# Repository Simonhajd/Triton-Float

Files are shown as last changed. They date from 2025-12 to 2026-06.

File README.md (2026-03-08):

# Triton Float

Development repository for the 2026 Triton Robotics Float.

## Overview

The Triton Float is being developed for the 2026 MATE ROV Pioneer competition (Newfoundland).
This design iteration is approximately 33% smaller than last year's model, while targeting more than 2× performance improvements in speed and significantly increased precision through layered redundancy and sensor feedback systems. It also includes a dedicated LoRa radio as opposed to last year's 4cm wire antenna, which will increase the reliability and robustness of the system.

## Features

Dimensions: 200mm x 4 in diameter.
Buoyancy system: PWM pump ranging from 220mL/min to -220mL/min.

Accuracy Strategy:

- Internal pressure sensor for ballast state verification  
- Pump movement feedback sensor for closed-loop control  
- Pre-calibrated pump flow rate modeling for predictive adjustment
- Additional onboard MCU sensors for reproducible control accuracy

## Hardware / Electrical

- Microcontroller: XIAO nRF52840 Sense  

- Sensors:  
  - XIAO nRF52840 Sense onboard IMU & sensors  
  - Blue Robotics Bar02  
  - Internal pressure sensor  
  - Pump movement sensor  

- Power System:  
  Custom voltage regulation system controlled via relay and magnetic hall-effect sensor on a secondary accessory PCB  

- PCB Revisions:  
  R2 completed, R3 in development

## Mechanical Design

Fusion / CAD link:
🔗 [View Fusion 360 CAD](https://a360.co/4slAPcB)

Notes:
### Structural Considerations:

Cylindrical housing designed to fit within a 4 in diameter constraint

Internal layout arranged to allow operation in the case of flooding (up to ~50-75% of internal volume) while maintaining core electronic functionality.

PCB mounted using tight-tolerance standoffs to prevent movement under vibration and ease serviceability

Layer system used to keep the float intact when the top flange and shell is removed.

### Integration Notes:

Limited internal volume required careful routing of wiring and tubing

Added solderable vias for power, in order to have a secure connection to the battery.

Accessory PCB used to isolate power regulation from main control logic

R3 revision addresses footprint issues and uses a different simpler power system for a working prototype.

## Current Status

- Version / Revision: R2
- In progress: R3, with fixed tracing and the internal pressure sensor.
- Completed: R2.
- Next steps: Testing R3 when it comes in.

## Tools 

- PCB software: KiCad
- CAD software: Fusion 360
- Firmware tools: C++

## Images
Screenshot 2026-02-16 at 4 56 35 PM

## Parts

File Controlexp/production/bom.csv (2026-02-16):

Designator | Footprint | Quantity | Value | LCSC Part #
C1, C3, C7 | 0805 | 3 | 0.1uF
C2, C4, C8 | 0805 | 3 | 10uF
C5 | 0805 | 1 | 10uF, 25V
C6 | 0805 | 1 | 22uF, 6.3V
D1 | 0805 | 1 | RED
J1 | CONN_RF2-04A-T-00-50-G_ADM | 1 | SMA_CONNECTOR
J4 | MOLEX_530470510 | 1 | 530470510
J5 | PinHeader_1x05_P2.54mm_Vertical | 1 | Power Connector
J6 | JST_GH_BM04B-GHS-TBT_1x04-1MP_P1.25mm_Vertical | 1 | Pressure sensor
J7 | PinHeader_1x03_P2.54mm_Vertical | 1 | POWER PROBE
L1 | 0805 | 1 | 2.2uH
R1, R2 | 0805 | 2 | 10k
R3 | 0603 | 1 | 220
R5, R6 | 0603 | 2 | 4.7k
U2 | HOPERF_RFM9XW_THT | 1 | RFM95W
U3 | WSON-8-1EP_2x2mm_P0.5mm_EP0.9x1.6mm_ThermalVias | 1 | TPS62162DSG
U4 | Bosch_LGA-8_3x3mm_P0.8mm_ClockwisePinNumbering | 1 | BME680
U5 | MODULE_113991054 | 1 | XIAO-nRF52840-DIP

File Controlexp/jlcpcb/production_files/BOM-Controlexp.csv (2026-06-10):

Comment | Designator | Footprint | LCSC | Quantity
2.2uH | L2 | L_0805_2012Metric |  | 1
SS34 | D2 | DIOM7959X265N |  | 1
Conn_01x02 | J2 | P-250-202 |  | 1
0.1uF | C1 | C_0805_2012Metric |  | 1
RED | D1 | LED_0805_2012Metric |  | 1
2.2uH | L1 | L_0805_2012Metric |  | 1
10uF | C2 | C_0805_2012Metric |  | 1
530470510 | J4 | MOLEX_530470510 |  | 1
RFM95W |  | HOPERF_RFM9XW_THT |  | 0
Pressure sensor | J6 | JST_GH_BM04B-GHS-TBT_1x04-1MP_P1.25mm_Vertical |  | 1
4.7k | R6 | R_0603_1608Metric |  | 1
TPS62162DSG | U3 | WSON-8-1EP_2x2mm_P0.5mm_EP0.9x1.6mm_ThermalVias |  | 1
10uF | C4 | C_0805_2012Metric |  | 1
0.1uF | C3 | C_0805_2012Metric |  | 1
Conn_Coaxial_Small | J1 | CONN_RF2-04A-T-00-50-G_ADM |  | 1
22uF, 6.3V | C6 | C_0805_2012Metric |  | 1
10uF, 25V | C5 | C_0805_2012Metric |  | 1
4.7k | R5 | R_0603_1608Metric |  | 1
TPS62163DSG | U5 | WSON-8-1EP_2x2mm_P0.5mm_EP0.9x1.6mm_ThermalVias |  | 1
220 | R3 | R_0603_1608Metric |  | 1
220 uF | C9 | C_0805_2012Metric |  | 1
Extra sensor TOP | J10 | JST_GH_BM04B-GHS-TBT_1x04-1MP_P1.25mm_Vertical |  | 1
10uF, 25V | C11 | C_0805_2012Metric |  | 1
LED | J8 | JST_GH_BM04B-GHS-TBT_1x04-1MP_P1.25mm_Vertical |  | 1
100nF | C14 | C_0805_2012Metric |  | 1
Power Connector | J5 | PinHeader_1x05_P2.54mm_Vertical |  | 1
Conn_01x02 | JBUTT1 | PinHeader_1x02_P2.54mm_Vertical |  | 1
220 uF | C10 | C_0805_2012Metric |  | 1
ToF sensor | J7 | JST_GH_BM04B-GHS-TBT_1x04-1MP_P1.25mm_Vertical |  | 1
100nF | C13 | C_0805_2012Metric |  | 1
SN74LVC1T45DBV | U6 | SOT-23-6 |  | 1
BMP388 | U7 | XDCR_BMP388 |  | 1
PWRCONN | J9 | JST_GH_BM03B-GHS-TBT_1x03-1MP_P1.25mm_Vertical |  | 1
XIAO-ESP32-S3-Plus-SMD | U1 | XIAO-ESP32-S3-Plus-SMD |  | 1
22uF, 10V | C12 | C_0805_2012Metric |  | 1
Extra sensor BOTTOM | J11 | JST_GH_BM04B-GHS-TBT_1x04-1MP_P1.25mm_Vertical |  | 1

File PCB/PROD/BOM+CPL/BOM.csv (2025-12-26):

BOM
BOM
BOM
FlightController
Id | Designator | Footprint | Quantity | Comment | Supplier and ref
1 | R3,R1 | R_0402_1005Metric_Pad0.72x0.64mm_HandSolder | 2 | 0.1uF
2 | R4,R2 | R_0402_1005Metric_Pad0.72x0.64mm_HandSolder | 2 | 10uF

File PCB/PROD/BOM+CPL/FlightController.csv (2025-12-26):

Id | Designator | Footprint | Quantity | Designation | Supplier and ref
1 | R3,R1 | R_0402_1005Metric_Pad0.72x0.64mm_HandSolder | 2 | 0.1uF
2 | R4,R2 | R_0402_1005Metric_Pad0.72x0.64mm_HandSolder | 2 | 10uF
3 | R5 | R_0402_1005Metric_Pad0.72x0.64mm_HandSolder | 1 | 10-33 uF
4 | U1 | XIAO-nRF52840-DIP | 1 | nRF52840 (Sense) WAS HERE
5 | U2 | XCVR_RFM95W-868S2 | 1 | RFM95W
6 | J6 | PinHeader_1x03_P2.54mm_Vertical | 1 | Connect The Hall Circuit Here!
7 | J5 | PinHeader_1x05_P2.54mm_Vertical | 1 | Feedback This Side
8 | J4 | PinHeader_1x03_P2.54mm_Vertical | 1 | BATT Reg IC
9 | J3 | PinHeader_1x01_P2.54mm_Vertical | 1 | -
10 | J2 | PinHeader_1x01_P2.54mm_Vertical | 1 | +
11 | TS Better Work | TE_5-1814832-2 | 1 | SMA Connector

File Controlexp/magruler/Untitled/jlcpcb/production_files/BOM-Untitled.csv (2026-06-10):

Comment | Designator | Footprint | LCSC | Quantity
TMAG5273A1QDBVR | U2 | DBV0006A-IPC_A |  | 1
100nF | C3 | C_0201_0603Metric |  | 1
100nF | C2 | C_0201_0603Metric |  | 1
Conn_01x04_Pin | J1 | JST_GH_BM04B-GHS-TBT_1x04-1MP_P1.25mm_Vertical |  | 1
TMAG5273A1QDBVR | U4 | DBV0006A-IPC_A |  | 1
TMAG5273A1QDBVR | U3 | DBV0006A-IPC_A |  | 1
220 | R3 | R_0603_1608Metric |  | 1
RED | D1 | LED_0805_2012Metric |  | 1
100nF | C1 | C_0201_0603Metric |  | 1

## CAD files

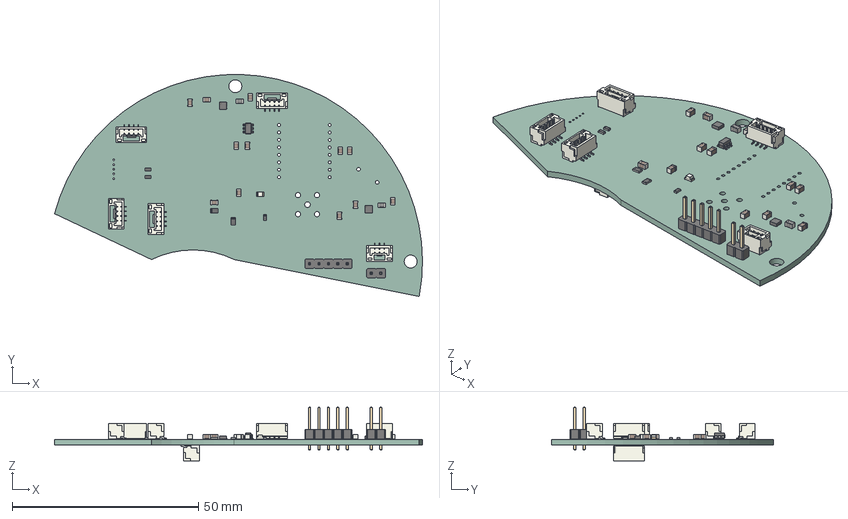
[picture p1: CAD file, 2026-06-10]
Controlexp/.step
98.7 x 59.5 x 14.4 mm
L_0805_2012Metric x 2
C_0805_2012Metric x 12
R_0805_2012Metric x 2
JST_GH_BM04B-GHS-TBT_1x04-1MP_P1.25mm_Vertical x 5
R_0603_1608Metric x 3
WSON-8-1EP_2x2mm_P0.5mm_EP0.9x1.6mm x 2
LED_0805_2012Metric
PinHeader_1x05_P2.54mm_Vertical
PinHeader_1x02_P2.54mm_Vertical
SOT-23-6
JST_GH_BM03B-GHS-TBT_1x03-1MP_P1.25mm_Vertical
Controlexp_PCB

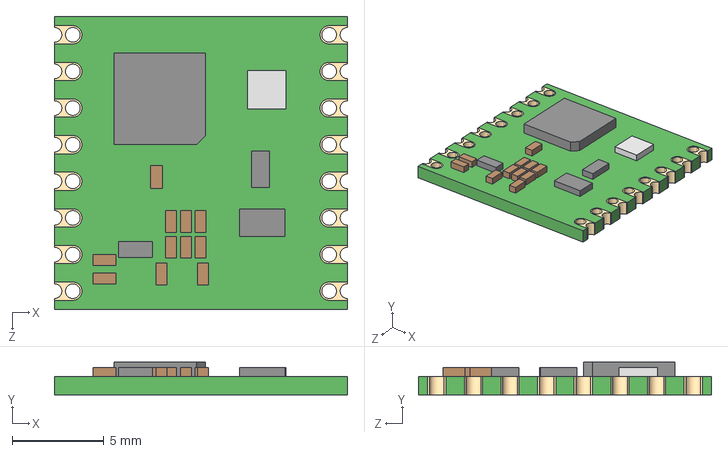
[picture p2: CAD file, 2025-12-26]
PCB/Symbols+Footprints/RFM95W_868S2/RFM95W-868S2.step
16.0 x 1.80 x 16.0 mm

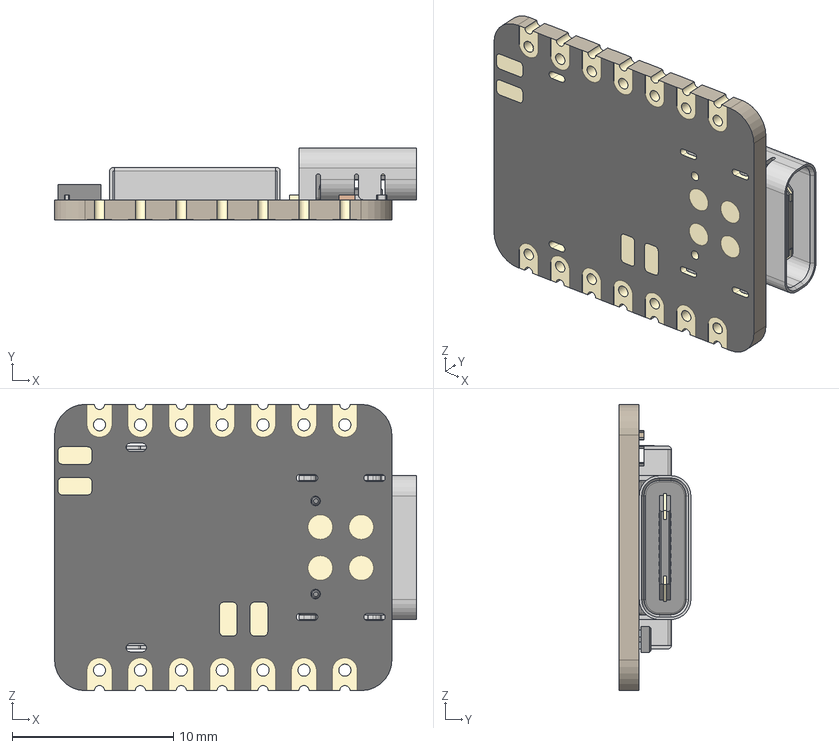
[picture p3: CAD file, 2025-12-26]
PCB/Symbols+Footprints/SeeedStudio_XIAO_nRF52840_v1.1_KiCAD/XIAO-nRF52840 v15.step
22.5 x 4.46 x 17.8 mm
BOSS-EXTRUDE14_8_
BOSS-EXTRUDE7_4_
BOSS-EXTRUDE7_3_
BOSS-EXTRUDE14_4_
BOSS-EXTRUDE14_2_
BOSS-EXTRUDE14_11_
BOSS-EXTRUDE7_7_
BOSS-EXTRUDE14_9_
BOSS-EXTRUDE14_3_
BOSS-EXTRUDE14_7_
MIRROR2
BOSS-EXTRUDE14_5_
BOSS-EXTRUDE14_12_
BOSS-EXTRUDE7_8_
BOSS-EXTRUDE7_1_
BOSS-EXTRUDE14_10_
BOSS-EXTRUDE7_9_
BOSS-EXTRUDE14_6_
BOSS-EXTRUDE14_1_
BOSS-EXTRUDE7_6_
BOSS-EXTRUDE7_2_
CUT-EXTRUDE5
BOSS-EXTRUDE7_5_
Shield
Pins
CAP x 2
ANT1
Silkscreen
CAP 3
LED
USR
2 v1

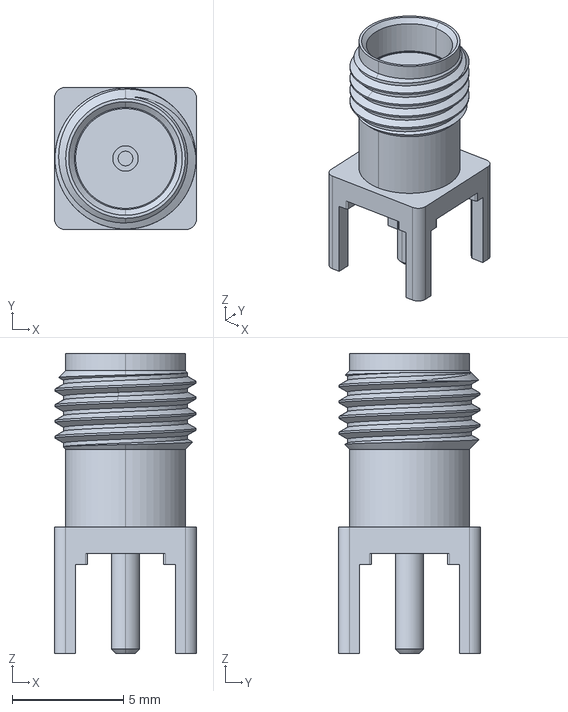
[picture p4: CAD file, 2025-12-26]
PCB/Symbols+Footprints/SMA/5-1814832-2.step
6.40 x 6.40 x 13.5 mm

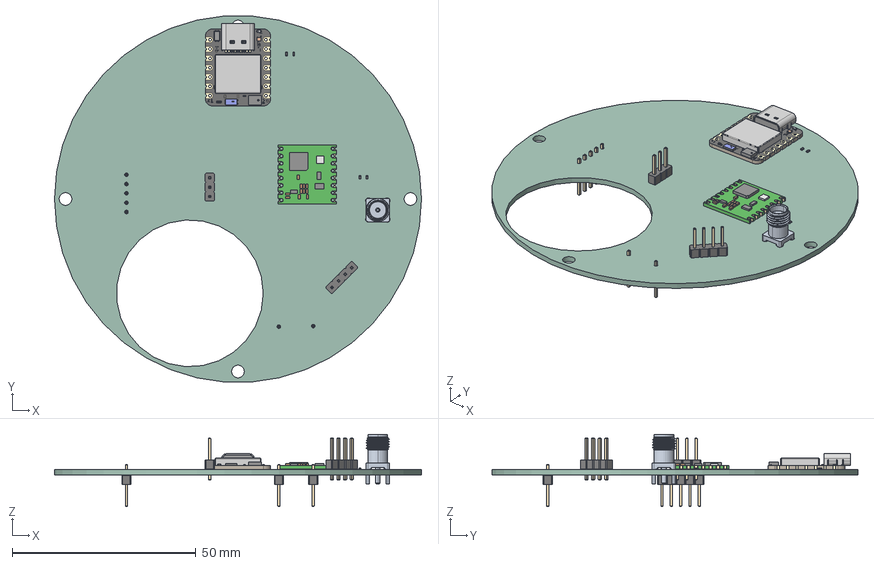
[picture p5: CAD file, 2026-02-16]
Controlexp/Controlexp.step
100.0 x 99.7 x 19.7 mm
BOSS-EXTRUDE14_8_
BOSS-EXTRUDE7_4_
BOSS-EXTRUDE7_3_
BOSS-EXTRUDE14_4_
BOSS-EXTRUDE14_2_
BOSS-EXTRUDE14_11_
BOSS-EXTRUDE7_7_
BOSS-EXTRUDE14_9_
BOSS-EXTRUDE14_3_
BOSS-EXTRUDE14_7_
MIRROR2
BOSS-EXTRUDE14_5_
BOSS-EXTRUDE14_12_
BOSS-EXTRUDE7_8_
BOSS-EXTRUDE7_1_
BOSS-EXTRUDE14_10_
BOSS-EXTRUDE7_9_
BOSS-EXTRUDE14_6_
BOSS-EXTRUDE14_1_
BOSS-EXTRUDE7_6_
BOSS-EXTRUDE7_2_
CUT-EXTRUDE5
BOSS-EXTRUDE7_5_
Shield
Pins
CAP x 2
ANT1
Silkscreen
CAP 3
LED
USR
2 v1
R_0402_1005Metric x 4
PinHeader_1x04_P2.54mm_Vertical
RFM95W-868S2
PinHeader_1x03_P2.54mm_Vertical
PinHeader_1x01_P2.54mm_Vertical x 2
PinHeader_1x05_P2.54mm_Vertical
FlightController_PCB

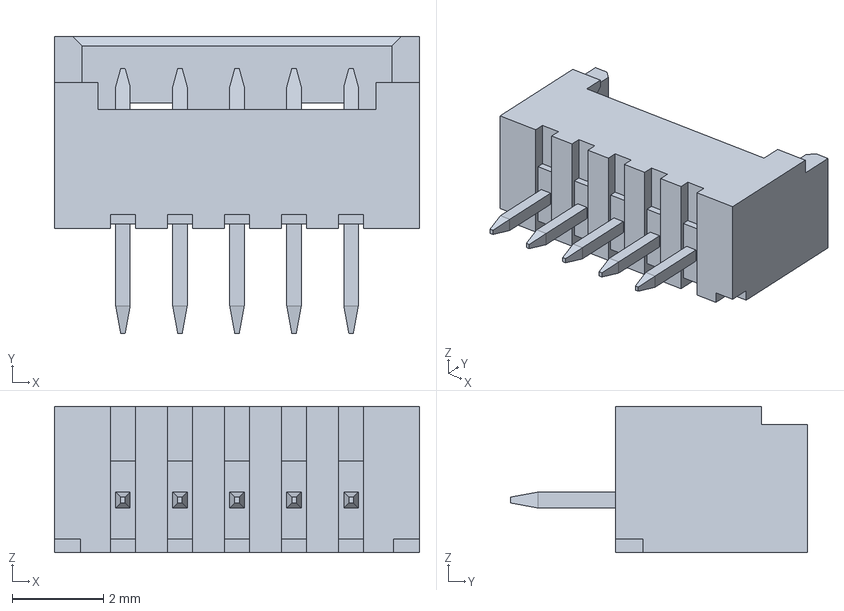
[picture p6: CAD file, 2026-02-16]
PCB/Symbols+Footprints/530470510/530470510.step
8.00 x 6.50 x 3.20 mm

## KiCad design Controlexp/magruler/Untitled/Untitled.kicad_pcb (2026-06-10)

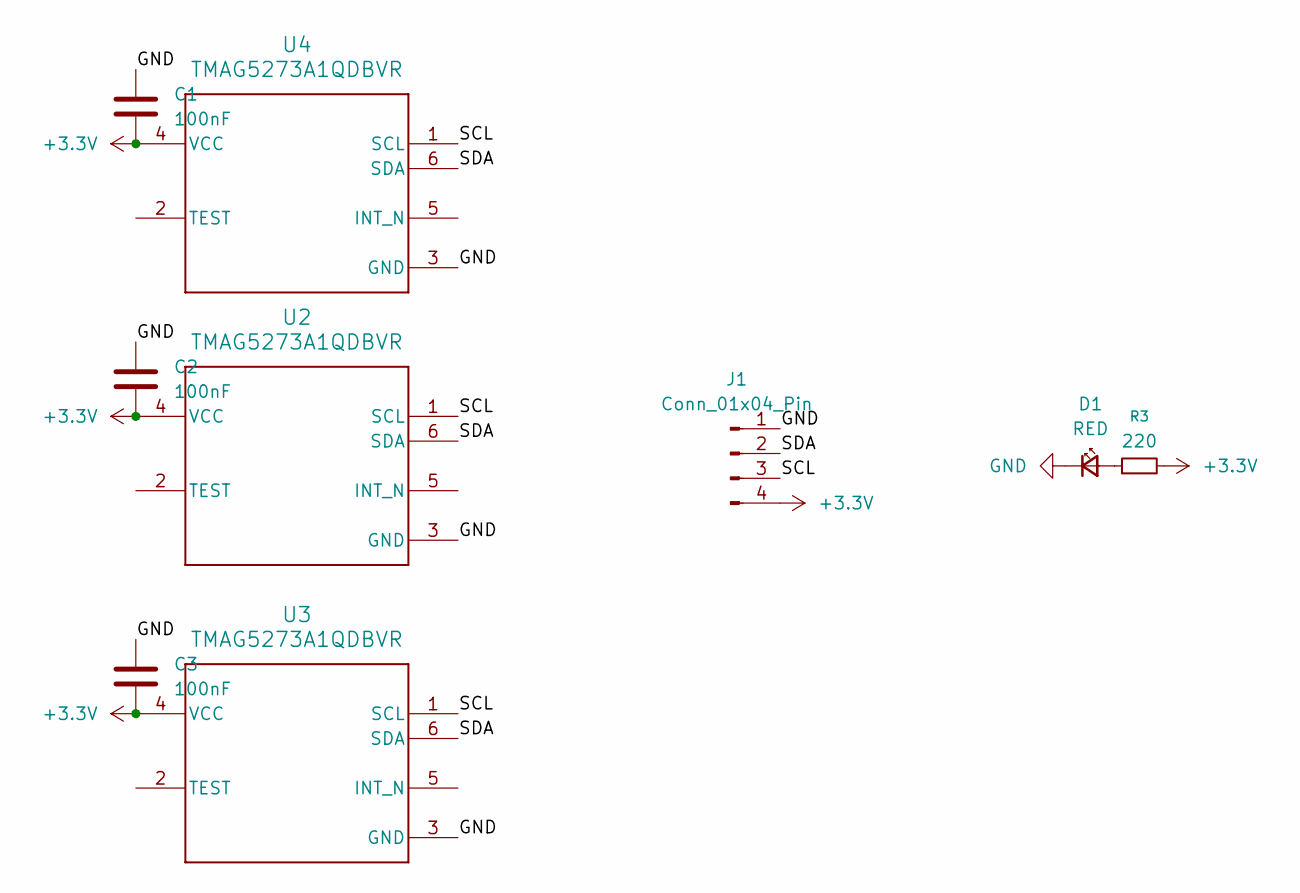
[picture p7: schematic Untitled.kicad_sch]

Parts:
C1, C2, C3: 100nF; C_0201_0603Metric
D1: RED; LED_0805_2012Metric
J1: Conn_01x04_Pin; JST_GH_BM04B-GHS-TBT_1x04-1MP_P1.25mm_Vertical
R3: 220; R_0603_1608Metric
U2, U3, U4: TMAG5273A1QDBVR; DBV0006A-IPC_A

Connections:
+3.3V: C1.2, C2.2, C3.2, J1.4, R3.2, U2.4 (VCC), U3.4 (VCC), U4.4 (VCC)
/SCL: J1.3, U2.1 (SCL), U3.1 (SCL), U4.1 (SCL)
/SDA: J1.2, U2.6 (SDA), U3.6 (SDA), U4.6 (SDA)
GND: C1.1, C2.1, C3.1, D1.1 (K), J1.1, U2.3 (GND), U3.3 (GND), U4.3 (GND)
unnamed: D1.2 (A), R3.1

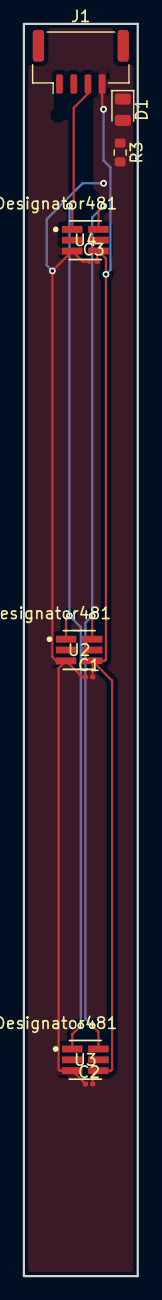
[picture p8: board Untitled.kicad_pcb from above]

Board: 2 copper layers, 10.0 x 110.0 mm, 9 parts (0 on the bottom side), 5 nets.

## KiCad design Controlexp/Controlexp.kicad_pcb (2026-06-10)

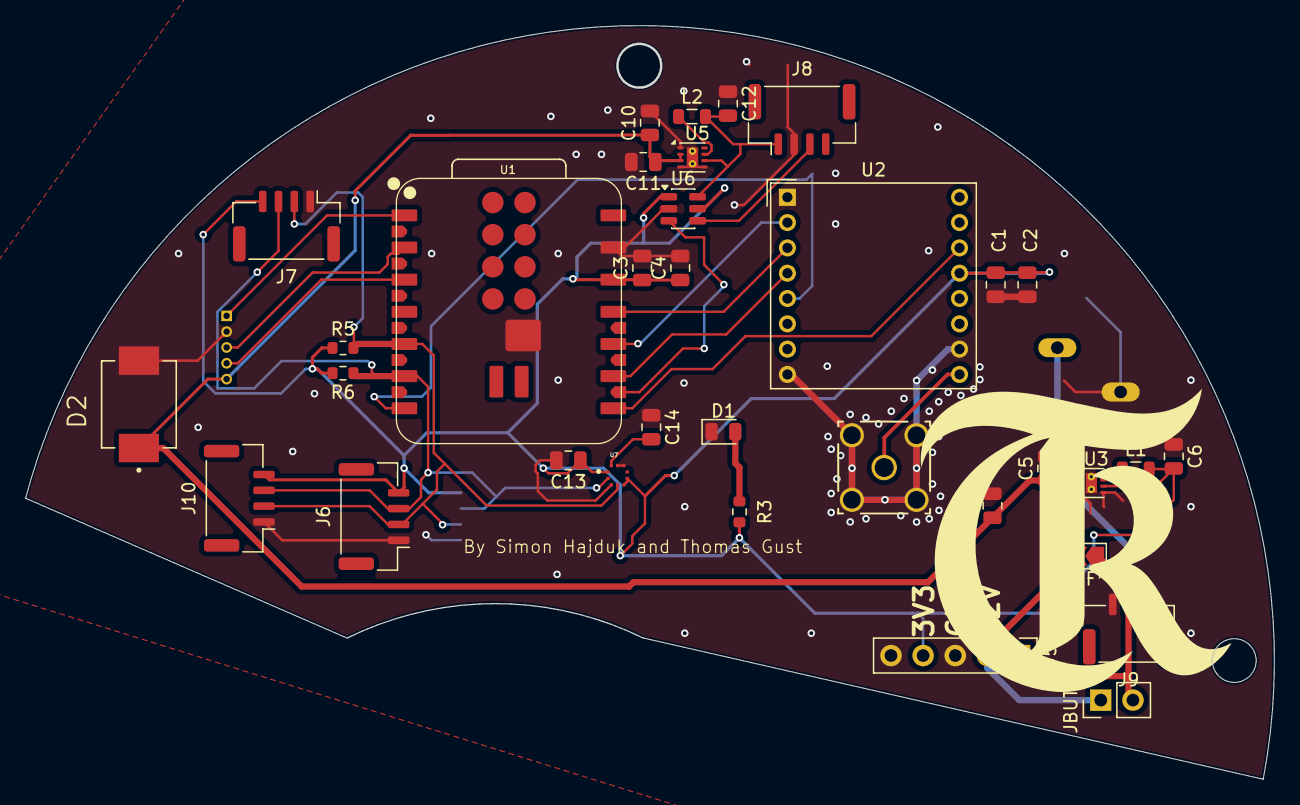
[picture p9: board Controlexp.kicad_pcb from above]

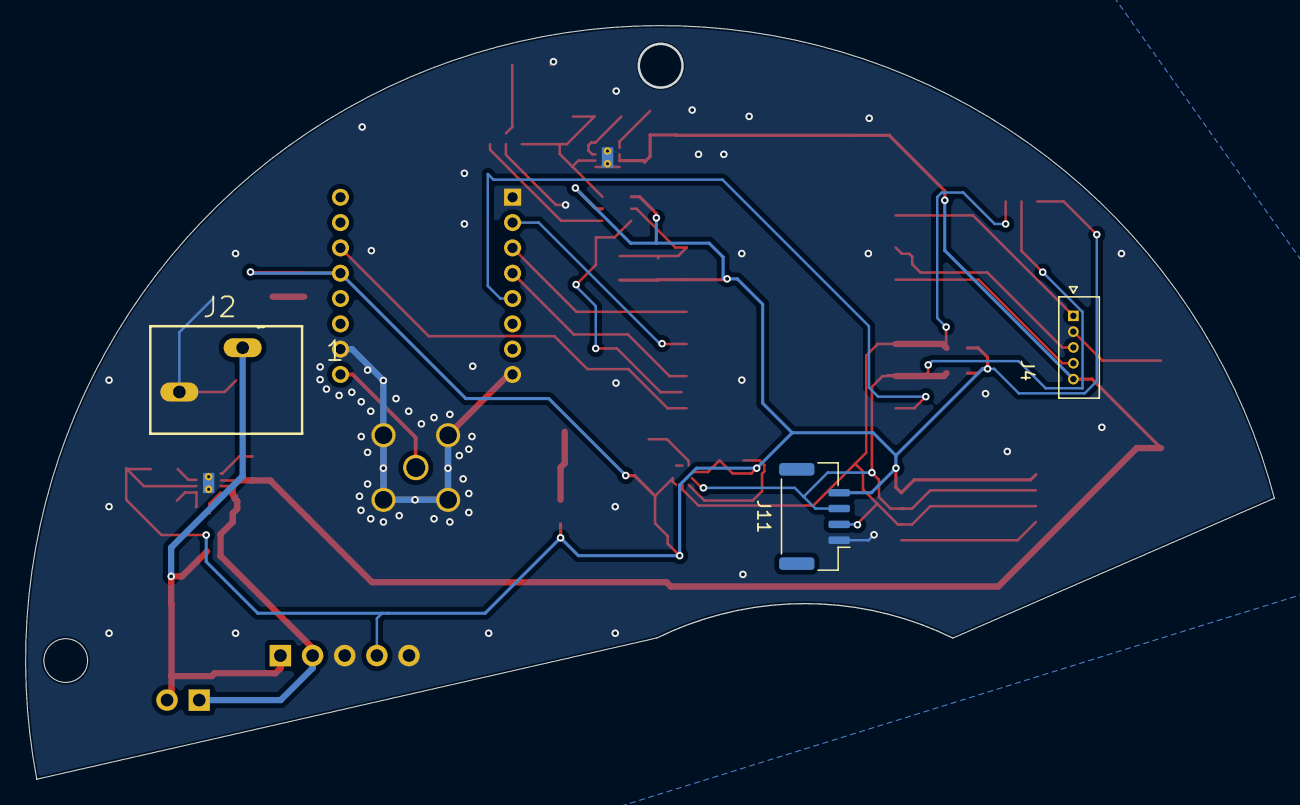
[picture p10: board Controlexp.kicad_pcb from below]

Board: 2 copper layers, 98.7 x 59.5 mm, 36 parts (3 on the bottom side), 21 nets.

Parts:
C1, C3: 0.1uF; C_0805_2012Metric
C2, C4: 10uF; C_0805_2012Metric
C5, C11: 10uF, 25V; C_0805_2012Metric
C6: 22uF, 6.3V; C_0805_2012Metric
C9, C10: 220 uF; C_0805_2012Metric
C12: 22uF, 10V; C_0805_2012Metric
C13, C14: 100nF; C_0805_2012Metric
D1: RED; LED_0805_2012Metric
D2: SS34; DIOM7959X265N
J1: Conn_Coaxial_Small; CONN_RF2-04A-T-00-50-G_ADM
J2: Conn_01x02; P-250-202
J4: 530470510; MOLEX_530470510
J5: Power Connector; PinHeader_1x05_P2.54mm_Vertical
J6: Pressure sensor; JST_GH_BM04B-GHS-TBT_1x04-1MP_P1.25mm_Vertical
J7: ToF sensor; JST_GH_BM04B-GHS-TBT_1x04-1MP_P1.25mm_Vertical
J8: LED; JST_GH_BM04B-GHS-TBT_1x04-1MP_P1.25mm_Vertical
J9: PWRCONN; JST_GH_BM03B-GHS-TBT_1x03-1MP_P1.25mm_Vertical
J10: Extra sensor TOP; JST_GH_BM04B-GHS-TBT_1x04-1MP_P1.25mm_Vertical
J11: Extra sensor BOTTOM; JST_GH_BM04B-GHS-TBT_1x04-1MP_P1.25mm_Vertical
JBUTT1: Conn_01x02; PinHeader_1x02_P2.54mm_Vertical
L1, L2: 2.2uH; L_0805_2012Metric
R3: 220; R_0603_1608Metric
R5, R6: 4.7k; R_0603_1608Metric
U1: XIAO-ESP32-S3-Plus-SMD
U2: RFM95W; HOPERF_RFM9XW_THT
U3: TPS62162DSG; WSON-8-1EP_2x2mm_P0.5mm_EP0.9x1.6mm_ThermalVias
U5: TPS62163DSG; WSON-8-1EP_2x2mm_P0.5mm_EP0.9x1.6mm_ThermalVias
U6: SN74LVC1T45DBV; SOT-23-6
U7: BMP388; XDCR_BMP388

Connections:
+3.3V: C1.1, C2.1, C3.1, C4.1, C6.2, C13.1, J5.4, J6.4, J7.4, J10.4, J11.4, L1.2, R3.2, R5.2, R6.2, U1.12 (3V3), U2.13 (3_3V), U3.6 (VOS), U6.1 (VCCA), U6.5 (DIR), U7.1 (VDDIO), U7.5 (SDO), U7.6 (CSB)
+5V: C12.2, J8.1, L2.2, U5.6 (VOS), U6.6 (VCCB)
+12V: C5.1, C9.1, C10.1, C11.1, D2.C, J2.L1 (Pin_1), J4.5, J5.1, J5.2, J9.2, JBUTT1.1, JBUTT1.2, U3.2 (VIN), U3.3 (EN), U5.2 (VIN), U5.3 (EN)
/ANT: J1.1 (In), U2.9 (ANT)
/BMPSCL: J6.3, J7.3, J10.3, J11.3, R6.1, U1.6 (GPIO6_A5_D5_SCL), U7.2 (SCK)
/BMPSDA: J6.2, J7.2, J10.2, J11.2, R5.1, U1.5 (GPIO5_A4_D4_SDA), U7.4 (SDI)
/DIN: J8.3, U6.4 (B)
/DIR: J4.3, U1.2 (GPIO2_A1_D1)
/FEEDBACK: J4.4, U1.3 (GPIO3_A2_D2)
/INT: U1.8 (GPIO44_D7_RX), U2.14 (DIO0)
/LEDSERIAL: U1.21 (GPIO11_DVP_Y8_SPI_MOSI1), U6.3 (A)
/MISO: U1.10 (GPIO8_A9_D9_MISO), U2.2 (MISO)
/MOSI: U1.11 (GPIO9_A10_D10_MOSI), U2.3 (MOSI)
/NSS: U1.7 (GPIO43_D6_TX), U2.5 (NSS)
/PWM: J4.1, U1.1 (GPIO1_A0_D0)
/SCK: U1.9 (GPIO7_A8_D8_SCK), U2.4 (SCK)
GND: C1.2, C2.2, C3.2, C4.2, C5.2, C6.1, C9.2, C10.2, C11.2, C12.1, C13.2, C14.1, D1.1 (K), D2.A, J1.2 (Ext), J1.3 (GND), J1.4 (GND), J1.5 (GND), J2.L2 (Pin_2), J4.2, J5.3, J5.5, J6.1, J7.1, J8.2, J9.1, J9.3, J10.1, J11.1, U1.13 (GND), U1.34 (PAD), U2.1 (GND), U2.8 (GND@1), U2.10 (GND@2), U3.1 (PGND), U3.4 (AGND), U3.5 (FB), U3.9 (PAD), U5.1 (PGND), U5.4 (AGND), U5.5 (FB), U5.9 (PAD), U6.2 (GND), U7.3 (VSS), U7.8 (VSS), U7.9 (VSS)
unnamed: D1.2 (A), R3.1
unnamed: L1.1, U3.7 (SW)
unnamed: L2.1, U5.7 (SW)
unnamed: C14.2, U7.10 (VDD)

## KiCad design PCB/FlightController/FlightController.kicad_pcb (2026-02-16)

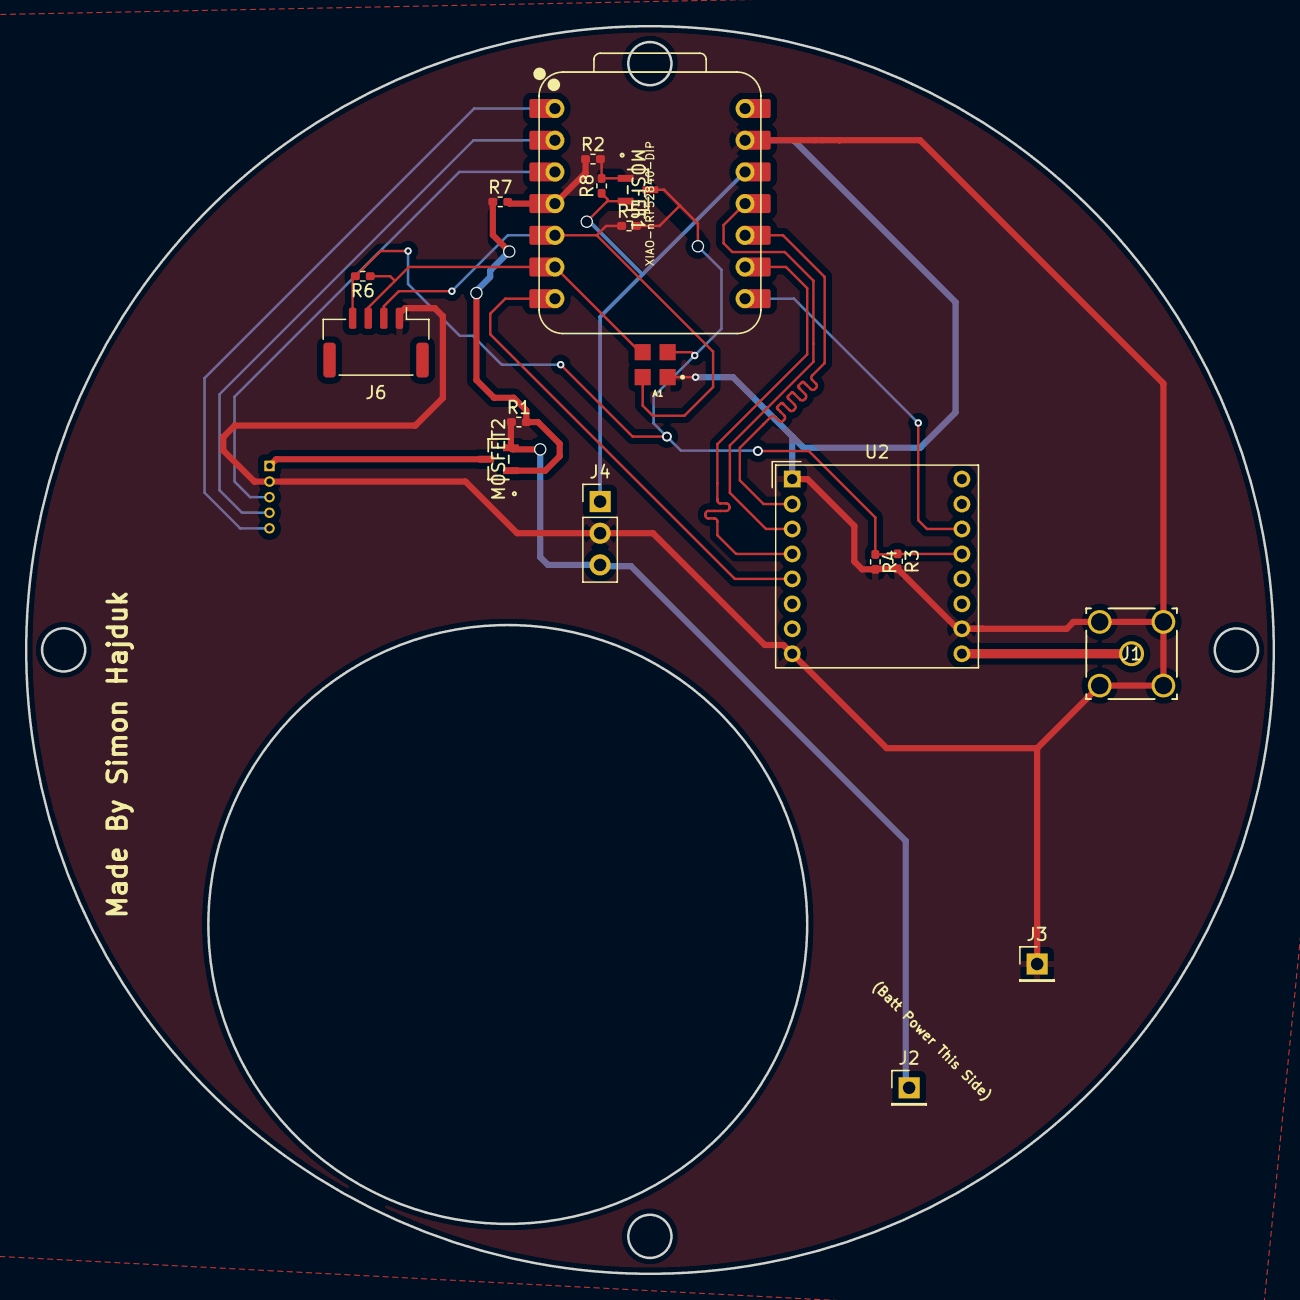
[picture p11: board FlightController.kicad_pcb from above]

Board: 2 copper layers, 100.0 x 100.0 mm, 19 parts (1 on the bottom side), 17 nets.

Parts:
A1: MS583702BA01-50; XDCR_MS583702BA01-50
J1: SMA Connector; CONN_RF2-04A-T-00-50-G_ADM
J2: BATT IN; PinHeader_1x01_P2.54mm_Vertical
J3: BATT OUT; PinHeader_1x01_P2.54mm_Vertical
J4: BATT Reg IC; PinHeader_1x03_P2.54mm_Vertical
J6: Pressure sensor; JST_GH_BM04B-GHS-TBT_1x04-1MP_P1.25mm_Vertical
J8: 530470510; MOLEX_530470510
MOSFET1, MOSFET2: DMP3068L-7; SOT-23_DMP3068L_DIO
R1, R2, R5, R6, R7: 4.7k; R_0402_1005Metric_Pad0.72x0.64mm_HandSolder
R3: 0.1uF; R_0402_1005Metric_Pad0.72x0.64mm_HandSolder
R4: 10uF; R_0402_1005Metric_Pad0.72x0.64mm_HandSolder
R8: 10k; R_0402_1005Metric_Pad0.72x0.64mm_HandSolder
U1: XIAO-nRF52840-DIP
U2: RFM95W; HOPERF_RFM9XW_THT

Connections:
ANT: J1.1, U2.9 (ANT)
DIR: J8.4, U1.2 (PA4_A1_D1)
FEEDBACK: J8.5, U1.1 (PA02_A0_D0)
GND: A1.1 (GND), J3.1, J4.2 (GND), J6.1, J8.2, R3.2, R4.2, U1.13 (GND), U2.1 (GND), U2.8 (GND@1), U2.10 (GND@2)
INT: U1.8 (PB09_A7_D7_RX), U2.14 (DIO0)
MAIN: J2.1, J4.3 (VIN), MOSFET2.2 (S), R1.1
MISO: U1.10 (PA5_A9_D9_MISO), U2.2 (MISO)
MOSI: U1.11 (PA6_A10_D10_MOSI), U2.3 (MOSI)
NSS: U1.7 (PB08_A6_D6_TX), U2.5 (NSS)
PWM: J8.3, U1.3 (PA10_A2_D2)
PWRSwitch: MOSFET1.1 (G), MOSFET2.1 (G), R1.2, R2.1, R2.2, R7.1, R7.2, R8.2, U1.4 (PA11_A3_D3)
RAWSWPOWER: J8.1, MOSFET2.3 (D)
SCK: U1.9 (PA7_A8_D8_SCK), U2.4 (SCK)
SCL: A1.3 (SCL), J6.3, R6.1, U1.6 (PA9_A5_D5_SCL)
SDA: A1.4 (SDA), J6.2, R5.1, U1.5 (PA8_A4_D4_SDA)
SW3v3: A1.2 (VDD), J6.4, MOSFET1.3 (D), R3.1, R4.1, R5.2, R6.2, U2.13 (3_3V)
VOUT: J4.1 (VOUT), MOSFET1.2 (S), R8.1, U1.12 (3V3)

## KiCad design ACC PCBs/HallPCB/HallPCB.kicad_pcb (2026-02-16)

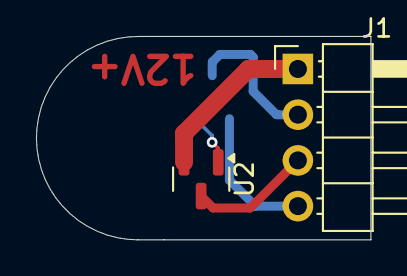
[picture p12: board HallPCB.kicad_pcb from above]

Board: 2 copper layers, 18.6 x 11.3 mm, 3 parts (1 on the bottom side), 5 nets.

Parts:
HALL: TLE49643MXTMA1; PG-SOT23-3-15_INF
J1: Conn_01x04_Socket; PinHeader_1x04_P2.54mm_Horizontal
U2: AP2127N-1.0; SOT-23

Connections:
GND: HALL.3 (GND), J1.2
MAIN: J1.1, U2.2 (VO)
RAWSWPOWER: J1.3, U2.3 (VI)
SIG: HALL.2 (Q), U2.1 (GATE)
VOUT: HALL.1 (VDD), J1.4

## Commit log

2025-12-26 Made the PCB
    [5-1814832-2.step, BOM.csv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]
2025-12-27 added a P-mosfet for the 3.3v wiring and let the 3.3v regulator "pre-power" the (now 4) pin switch system for the hall effect magnet sensor.
    added a P-mosfet for the 3.3v wiring and let the 3.3v regulator "pre-power" the (now 4) pin switch system for the hall effect magnet sensor.
    [FlightController.kicad_pcb, FlightController.kicad_sch, HallPCB.kicad_pcb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]
2025-12-27 All boards should be finished. ACC otw, and an earlier version of the main board otw
    [FlightController.kicad_pcb, FlightController.kicad_sch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]
2026-02-16 post R1 - flipped many traces and worked on adding an internal sensor for reduncancy
    [530470510.step, FlightController-Chipstyle.kicad_pcb, FlightController.kicad_pcb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]
2026-02-16 Initialize README.md with project details
    Added comprehensive details about the Triton Float project, including its overview, features, hardware specifications, mechanical design considerations, current status, tools used, and an optional im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
2026-02-16 add controlexp
    [Controlexp.kicad_pcb, Controlexp.kicad_sch, Controlexp.step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]
2026-02-19 lil fixes + sma gnd fix.
    Added gnd stitching and connected the sma gnd. and fixed some connections
    [Controlexp.kicad_pcb]
2026-06-10 fresh board
    [.step, BOM-Controlexp.csv, BOM-Untitled.csv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]
